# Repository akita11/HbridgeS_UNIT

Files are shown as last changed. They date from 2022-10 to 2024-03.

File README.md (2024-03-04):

# HbridgeS_UNIT

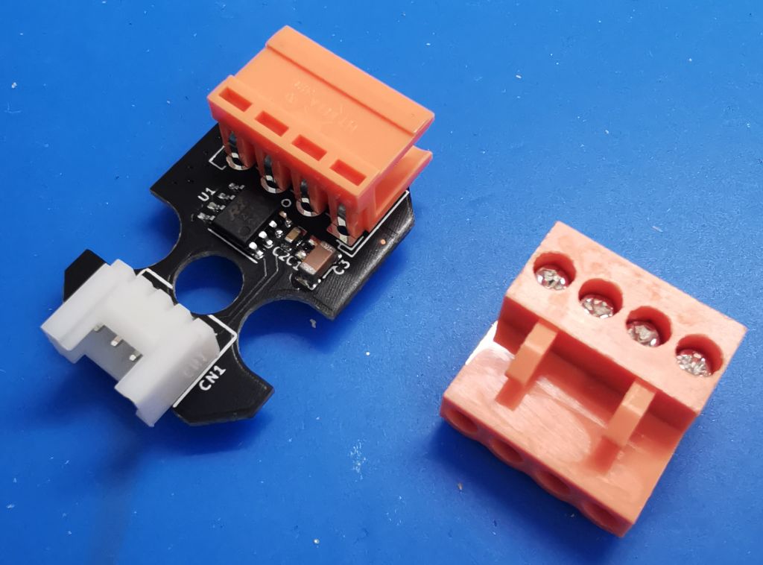
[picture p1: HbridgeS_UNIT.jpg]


DCモータなどの負荷の正転・逆転をGrove端子から制御できます。PWM制御を行うこともできます。負荷の電源はオレンジ色のコネクタ、またはGrove端子のVDDから選択できます。

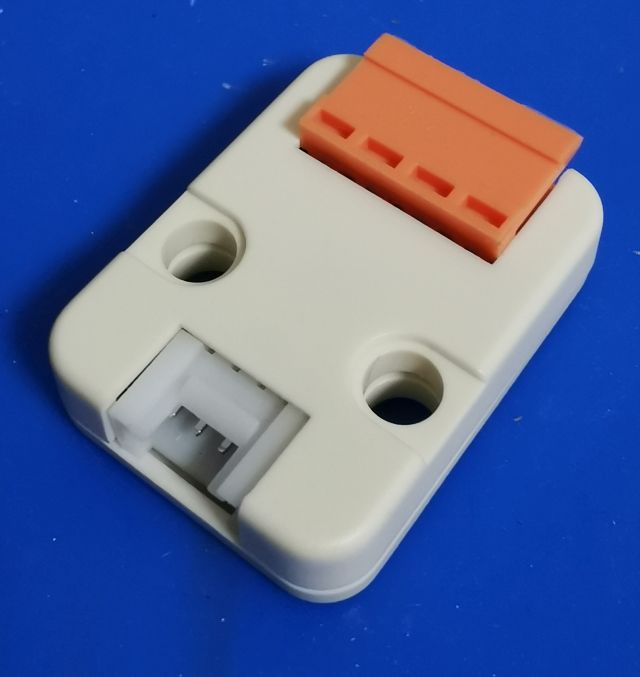
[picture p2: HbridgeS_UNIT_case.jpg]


基板形状が「[M5Stack用VH3.96-4ピンユニット](https://www.switch-science.com/products/4055)」と同一のため、そのケースを使うことができます。

Grove端子のVDDへの電源供給能力が不足する場合は[TypeC2Grove UNIT](https://www.switch-science.com/products/8453)等を使用してください。

## 使い方

オレンジ色のコネクタ(VH3.96-4p)に、負荷用の電源と負荷（DCモータ等）を接続します。電源供給の方法によって、主に2通りの接続方法があります。

### 電源供給をACアダプタ等から行う場合

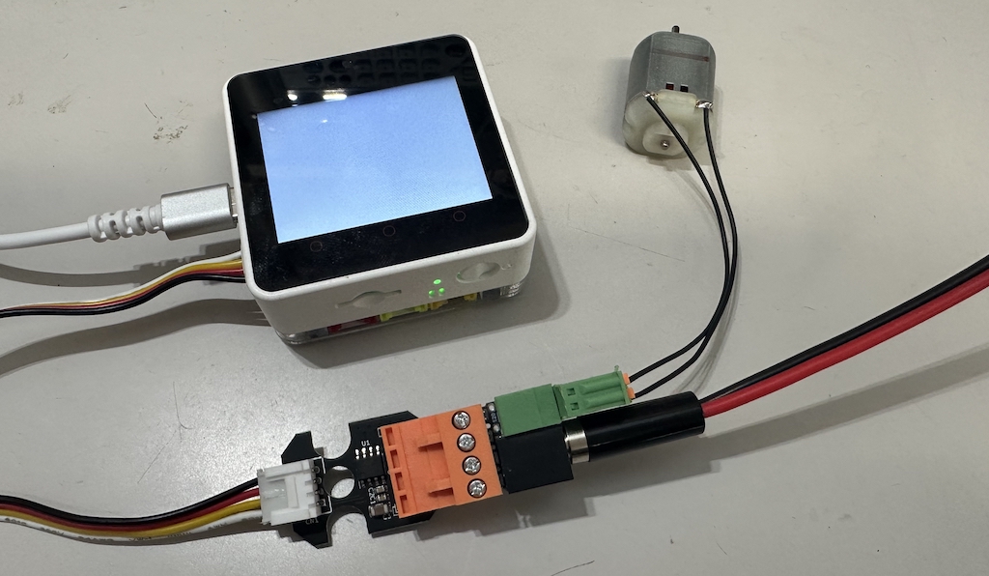
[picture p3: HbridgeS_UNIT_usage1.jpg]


オレンジ色のコネクタの電源（VM-G間）に、負荷に応じた電圧をACアダプタ等から供給します。また負荷をA-B間に接続します。（M5Stackの[BAVGソケット](https://www.switch-science.com/products/7234)を使うと、電源は2.1mmプラグ、負荷はスプリング端子で接続できて便利です）

### 電源供給をGrove端子から行う場合

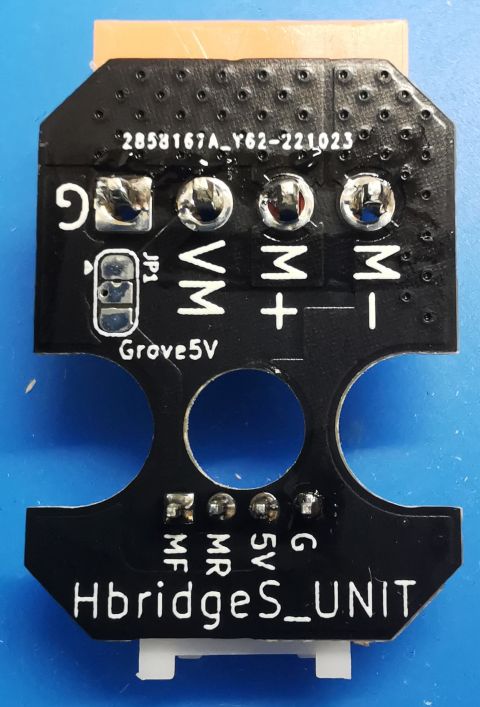
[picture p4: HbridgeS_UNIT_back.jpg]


裏面のJP1の、中央-上側の端子がつながっていますので、カッター等でカットし、中央と反対側の"Grove5V"側を、ハンダを盛るなどしてショートします。これによって、負荷への電源がGrove側の+5Vから供給されます。

ただし、一般にDCモータ等の負荷は消費電流が多く、マイコン側の+5V電源の供給能力が不足する場合がほとんどです。そのような場合は、[TypeC2Grove UNIT](https://www.switch-science.com/products/8453)を使用して、負荷側の電源をUSB Type-C端子から供給することができます。別途USB-CコネクタのACアダプタ等を接続してください。

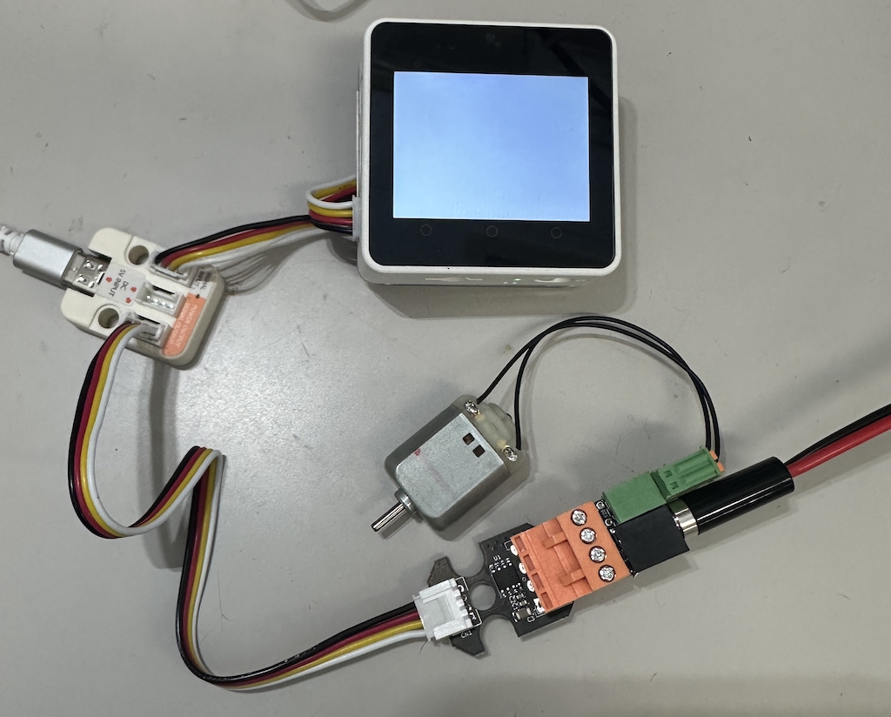
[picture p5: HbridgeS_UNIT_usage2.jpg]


### マイコンからの制御方法

マイコン（M5Stack等）からの負荷の制御は、Grove端子の2本の信号線によって行います。

| MF | MR | 機能 |
|----|----|-----|
| 1  | 0  | 正転 |
| 0  | 1  | 逆転 |
| 0  | 0  | 開放 |
| 1  | 1  | 短絡（ブレーキ） |

UIFlowでの[使用例](Hbrige_test.m5f)（以下）を参考にしてください。（Core2のPortAに接続した場合。MF=GPIO32、MR=GPIO33）

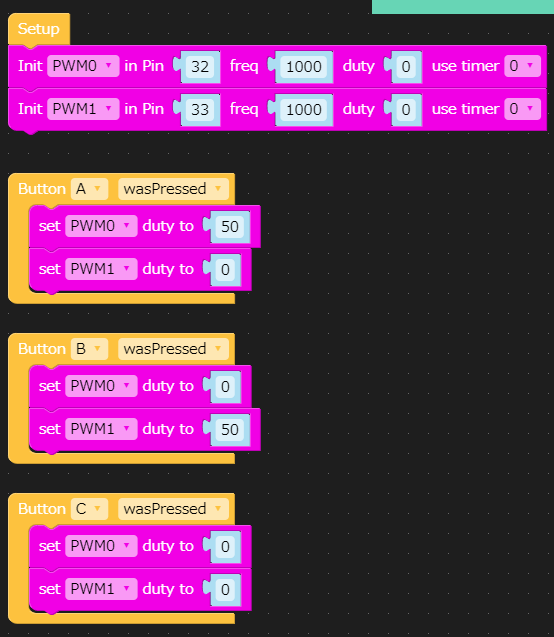
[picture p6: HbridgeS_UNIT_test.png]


## 仕様・制限事項

使用しているモータドライバ（[RZ社RZ7899](http://www.rz-mic.com/uploadfile/fj/201810310633.pdf)）の仕様から、負荷は以下の条件で使用してください。

- 負荷用電源電圧: 3〜25V
- 負荷電流: 5A（負荷電流に応じて放熱が必要となります）

## Author

Junichi Akita (akita@ifdl.jp, @akita11)

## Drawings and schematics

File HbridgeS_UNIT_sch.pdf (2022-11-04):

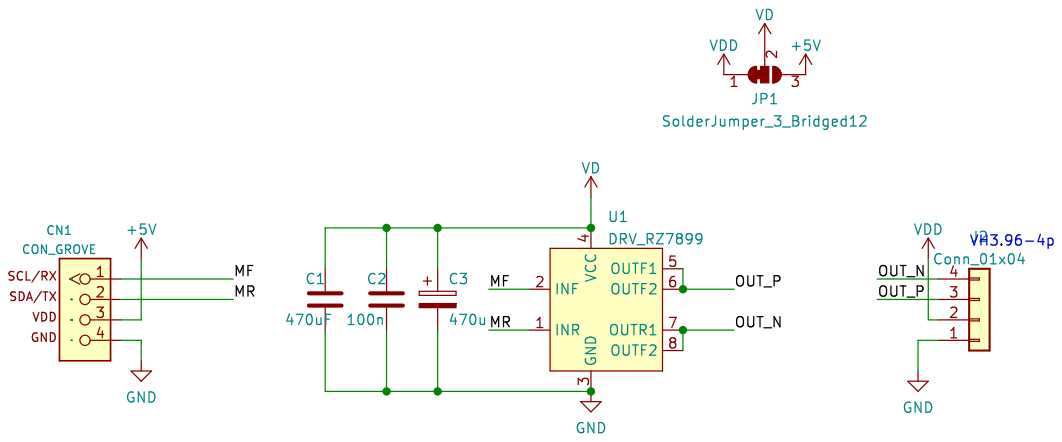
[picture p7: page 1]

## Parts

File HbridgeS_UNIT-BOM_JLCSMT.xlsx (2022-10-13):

Comment | Designator | Footprint | JLCPCB Part #（optional）
10u | C1 | C_0603_1608Metric | C85713
100n | C2 | C_0603_1608Metric | C282519
10uF/50V | C3 | C_1206_3216Metric | C13585
RZ7899 | U1 | SOIC-8_3.9x4.9mm_P1.27mm | C92373
